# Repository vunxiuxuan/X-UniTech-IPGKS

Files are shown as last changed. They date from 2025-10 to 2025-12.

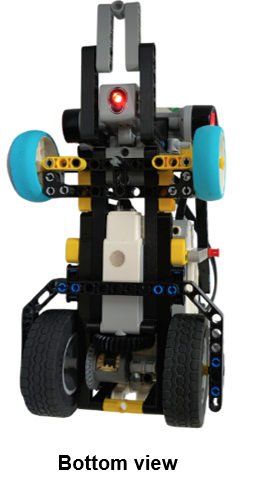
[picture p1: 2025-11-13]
v-photos/Bottom.png

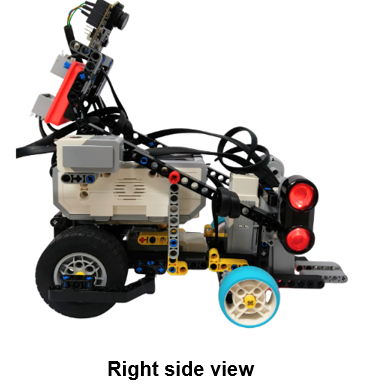
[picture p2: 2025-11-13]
v-photos/Right.png

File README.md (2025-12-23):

# Content (GitHub)
**schemes** This folder contains one or several schematic diagrams in the form of JPEG, PNG, or PDF of the electromechanical components illustrating all the elements (electronic components and motors) used in the vehicle and how they connect. This folder also included the schematic diagram of the robot for both open and obstacle challenge.

**src** This folder contains all the programming flowcharts and all programming used to participate in the WRO 2025 Future Engineers Category.

**t-photos** This folder contains photos of the team participating in the WRO 2025 Future Engineers Category.

**v-photos** This folder contains photos of the vehicle from all sides (top view, bottom view, front view, back view and side views)

**video** This folder contains video.md file that demonstrates how the robot functions to solve both challenges.

**models** This folder contains the robot building insturction and the 3D printed part building instruction that installed on the vehicle. The file is presented in .lxf, .ldr and .ldr format.

**other** This folder contains other files which can be used to understand how to prepare the vehicle for the competition.

Here attached with the link for our **COMPLETE DOCUMENTATION MODULE** (https://drive.google.com/file/d/107QRZqFFLUvLz7qMj4gl7RzuqnLO4l_k/view?usp=sharing)

# Table of Contents (Essay)
- [Introduction](#introduction)
- [X-UniTech Team, Malaysia](#x-unitech-team-malaysia)

- [1.0 Mobility Management](#10-mobility-management)
  - [1.1 Design of the self-driving car](#11-design-of-the-self-driving-car)
  - [1.2 Chassis of the self-driving car](#12-chassis-of-the-self-driving-car)

- [2.0 Power and Sense Management](#20-power-and-sense-management)
  - [2.1 Power source](#21-power-source)
  - [2.2 Sensor](#22-sensor)
  - [2.3 Build Of Materials (BOM)](#23-build-of-materials-bom)
  - [2.4 Wiring diagram](#24-wiring-diagram)

- [3.0 Obstacles Management](#30-obstacles-management)
  - [3.1 Open Challenge](#31-open-challenge)
  - [3.2 Obstacle Challenge](#32-obstacle-challenge)

- [4.0 Engineering Factors](#40-engineering-factors)
  
- [5.0 Improvements and Enhancements](#50-improvements-and-enhancements)
  - [5.1 Robot Construction](#51-robot-construction)
  - [5.2 Robot Programming](#52-robot-programming)

- [Credits](#credits)

# Introduction
This engineering documentation details comprehensive aspects of the car’s mobility management, power and sensor systems, obstacle detection and avoidance, construction design, integration of third-party sensors, and the improvements that were made throughout our preparation for the **World Robot Olympiad (WRO) International Final in Singapore 2025** under the Future Engineers Category.

# X-UniTech Team, Malaysia
X-UniTech is a team from Malaysia consisting of three-member engineering team specializing in the development of autonomous vehicles. Our team is responsible for the end-to-end design, construction, and integration of the vehicle's mechanical and electronic systems to ensure optimal performance. Let’s meet our members:

**Vun Xiu Xuan, Alvin Kong Wei Ee, and Grace Tan Hong Hui.**

Team Photo

# 1.0 Mobility Management
This section details the **mechanical design and propulsion system of our autonomous vehicle.** It covers the **chassis construction, component layout, and the integration of the motors.** Additionally, it introduces the fundamental engineering principles of speed, torque, and power that govern the vehicle's performance.

## 1.1 Design of the self-driving car
The autonomous self-driving car chassis and mechanical structure are built using the **Lego 45544 Mindstorms EV3 Education Set and various third-party sensors** such as **Pixy2 Camera** and **EV3 Multiplexer.**

Lego 45544 Mindstorms EV3 Education Set

The figures below show the autonomous vehicle we designed and constructed.  

**Top view**	

Robot (Top View)

**Bottom view** 

Robot (Bottom View)

**Front view**	

Robot (Front View)

**Back view** 

Robot (Back View)

**Left side view**	

Robot (Left Side View)

**Right side view** 

Robot (Right Side View)

## 1.2 Chassis of the self-driving car
The self-driving car chassis is designed to provide **structural support** and maintain **stability**, especially during high-speed maneuvers like sharp turns and rapid acceleration.

**(i) Selection of tyre**

For the front steering axle, we selected the **Medium Azure Hard Tyre** from the **Spike Essential** set because of its **hard rubber compound** that minimizes bouncing, allowing the vehicle **to track in a straight line** more reliably compared to softer tyres. The tyre's smaller diameter enables smoother and more precise steering corrections.

Medium Azure Hard Tyres

The rear axle is fitted with **LEGO MINDSTORMS EV3 tyres** (62.4 x 20 mm) on 43.2 mm rims. These tyres were selected for the excellent traction their tread pattern provides on typical competition surfaces, such as floors and mats. This high-grip design prevents wheel slippage during rapid acceleration and high-speed cornering. 

Lego Mindstorms EV3 Tyres

**(ii) Implementation of motor and its engineering principle**

Our self-driving car propulsion system consists of two EV3 Medium Motors mounted in a compact, orthogonal arrangement (one horizontal, one vertical). This design offers several key advantages: it optimizes internal space, simplifies the gear train assembly, and contributes to a low center of gravity. A low center of gravity is crucial for maintaining stability during the high-speed maneuvers required in the Open Challenge. 

EV3 Medium Motors

The diagram below illustrates the specifications and features of the EV3 Medium Motor.

Specifications of EV3 Medium Motor

The vehicle's steering mechanism is controlled by an **EV3 Medium Motor**, selected for its high responsiveness and precision. With a running torque of **8 Ncm** and a stall torque of **15 Ncm**, the motor provides ample force for steering control. Furthermore, its rotational speed of **260 rpm** allows quick rotations, making it well-suited for fine adjustments when avoiding traffic signs. 

 **(iii) Implementation of differential gear**
 
A differential gear is integrated into the drive axle, allowing the left and right wheels to **rotate at different speeds.** This mechanism is essential for executing smooth, controlled turns, as it prevents wheel binding and improves stability. This is particularly critical when navigating the tight corners found in the Open Challenge. Not only that, our robot also incorporates **a step-up gear ratio.** This setup makes the wheels spin **1.29 times faster** than the motor, increasing the speed from **260 RPM** at the motor to about **335 RPM** at the wheels. This helps the robot to move faster while at the same time maintaining stability during tight turns.

Differential Gear

**(iv) Engineering principle of steering**

The steering system is designed using **Ackermann steering geometry.** 

Ackermann Steering Geometry

This principle **turns the inner front wheel at a sharper angle** than the outer wheel, allowing both to follow ideal concentric turning circles. By minimizing lateral tire scrub, this geometry significantly reduces friction and wear. The primary benefits include enhanced cornering stability, improved traction, and the ability to execute sharp turns with greater precision.

**3D Printing Process Video**

3D Printing Process Video

https://youtu.be/b9eLe_nYFe0

# 2.0 Power and sense management
This section details the vehicle's **power source** and **sensor systems.** It covers the selection **rationale** and **implementation** of each sensor, along with an **analysis** of the **system's power consumption.** A **complete Build of Materials (BOM)** and **wiring diagram** are also provided for reference.

## 2.1 Power Source
The self-driving car is powered by a **Soshine 1.5V AA rechargeable lithium-ion (Li-ion) battery** with an energy capacity of 2600 mWh. This battery technology was selected for its stable voltage output, which ensures consistent and reliable performance for all electronic components.

Soshine Rechargeable AA Lithium-Ion Battery

## 2.2 Sensor
The self-driving car is designed to handle the diverse requirements of the Open and Obstacle Challenges. It includes **one color sensor, two ultrasonic sensors, one gyro sensor, and a Pixy2 camera.** The diagram below illustrates the placement and integration of these components.

Sensors

**(i) Pixy2 camera** 

The Pixy2 camera serves as the primary vision system for the vehicle during the Obstacle Challenge. Its main function is real-time object detection, allowing it to simultaneously **identify and track the red and green pillars** while the vehicle is in motion. It also helps to scan the magenta-colored parking zone to ensure the vehicle avoids this restricted area while navigating the course. The Pixy2 camera is mounted at a **65° angle** to provide optimal visibility when tracking traffic signs.

Pixy2 Camera

65° Pixy2 Camera

**(ii) Gyro sensor**

One gyro sensor is used to support our self-driving car. During both Open and Obstacle Challenge, it helps to **measure angles** and **maintain the correct heading** while driving. The gyro sensor also helps the robot to **turn at accurate angle** after passing the edge of the inner wall. While the gyro sensor can sometimes display errors at startup due to calibration issues, we resolved this by performing a hard reset before each run.

Gyro Sensor

**(iii) Ultrasonic sensor**

Our self-driving car is equipped with **two EV3 ultrasonic sensors.** These sensors measure the distance between the robot and wall **to avoid collision towards the walls.** The sensors operate by emitting sound waves and calculating the time it takes for them to bounce back after hitting a wall. This data enables the self-driving car to navigate efficiently, make accurate turns, and aim to complete the Open Challenge in the shortest time possible.

Ultrasonic Sensor

**(iv) Color sensor**

The colour sensor is only used in the Obstacle Challenge to **determine when the self-driving car should turn.** In a **clockwise** direction, the car **turns right** whenever it detects an orange line, while in a **counterclockwise** direction, it **turns left** upon detecting a blue line. The sensor functions by measuring the intensity of light entering it, allowing the car to identify colour lines and determine whether it is moving clockwise or counterclockwise. 

Color Sensor

## 2.3 Build of materials (BOM)

The table below shows the Build of Materials (BOM) used to build the self-driving car, making sure each part matches the car’s needs and functions.

Build of Materials (1)

Build of Materials (2)

Build of Materials (3)

Build of Materials (4)

Build of Materials (5)

Build of Materials (6)

## 2.4 Wiring diagram
The wiring diagram below illustrates the **sensors’ power consumption** and shows how the **motors and sensors are connected** within our self-driving car to support the setups for both the Open Challenge and the Obstacle Challenge. 

**(i) Open challenge wiring diagram**

Open Challenge Wiring Diagram

**(ii) Obstacle challenge wiring diagram**

Obstacle Challenge Wiring Diagram

# 3.0 Obstacles Management
In our project, we utilize the Clev3r-Python programming language to operate the robot. The programming structure is divided into two main sections which is the **Open Challenge** and the **Obstacle Challenge.** This section includes a flowchart and an overview of the code used for both challenges. 

## 3.1 Open Challenge
To complete the open challenge, our robot uses two main sensors which is an **EV3 Gyro Sensor** and **two EV3 Ultrasonic Sensors** on both the left and right sides. Since both **EV3 Ultrasonic Sensors** share the same port, we use a **multiplexer** to allow the robot to read data from each one separately. The left ultrasonic sensor is connected to Channel 2 of the multiplexer, while the right ultrasonic sensor is connected to Channel 3.

Gyro Sensor and Ultrasonic Sensor

The **EV3 Ultrasonic Sensors** helps the car to measure the distance between the robot and the walls. By comparing readings from the left and right sensors, the robot can determine whether it should move clockwise or counter clockwise. These readings also help the robot adjust its steering to avoid collisions and stay at a safe distance from inner and the outer walls. Additionally, the **EV3 Gyro Sensors** monitor the robot’s heading, ensuring it maintains a straight path and performs accurate turns at the correct angle when turning. 

Determine Direction (1)

In a quick overview, when the robot starts, it **first checks and sets up all its sensors.** Next, it **resets its steering** before moving. The robot then uses a **PID control system** to ensure smooth and stable turns. A drive function controls its speed and distance based on sensor data. Finally, the **main program** combines all these functions, enabling the robot to **follow walls, make precise turns,** and **complete all laps** efficiently and accurately. Further explanations of each function and programming part are provided in the **3.1.1 section below.**

Diagram below shows the flowchart for Open Challenge: 

Open Challenge Flow Chart

## 3.2 Obstacle Challenge
To complete the **Obstacle Challenge,** our robot utilizes four sensors which is **one Pixy2 Camera, one gyro sensor, two ultrasonic sensors** on both the left and right sides and **one colour sensor.** Since both ultrasonic sensors need to be connected to the same port, we use the **multiplexer** so that the robot can read data from both of the sensors.

Sensors

The **Pixy2 Camera** is connected to port 1 and it helps to detect the presence of pillars and magenta parking lot during the round. Next, the **EV3 Gyro Sensor** that connected to port 2 helps to ensures that the robot does the accurate turns and keep the robot’s heading straight during the round. In addition, both of the **EV3 Ultrasonic Sensor** is connected to EV3 Brick port 3 via the multiplexer. They help to detect the presence of the inner and outer wall and prevent the robot from hitting into the wall. Lastly, we utilize the **EV3 Colour Sensor** to identify the coloured line on the map which is the orange and blue line. The identified colour allows the robot to know the direction accurately. For instance, if orange line is scanned first, the direction will be in clockwise direction.

Here is the quick overview about the program. When the robot begins, it first **resets its steering mechanism** to ensure it starts from a centred and accurate position. As the robot drives, a **PID steering control system** is used to maintain stable movement and the correction such as gyro correction and keeping optimum distances from the outer wall. During the round, the **Drive function** continuously combines inputs from pillar detection, wall tracking, and PID correction. The sensors such as Pixy 2 Camera allows the robot **to identify traffic sign accurately** and choose the correct avoidance direction. After completing its last sections in the loop 12, the robot will **reverse to hit the wall** and aligns with the parking area and finally **performing a side parking neatly into the magenta parking zone.**

Diagram below shows the flowchart for **Obstacle Challenge:** 

Obstacle Challenge Flow Chart

# 4.0 Engineering Factors
This section showcases our **custom-designed and third-party open-source parts** along with detailed explanations of all the components installed in the car. 

At first, our autonomous self-driving car is **primarily built using the LEGO Mindstorms Education EV3 Core Set 45544.** However, we encountered several limitations while preparing for both the Open and Obstacle Challenges. For example, our design required more sensor ports than the EV3 brick could support, the **Pixy2 Camera was unstable** due to weak mounting, and we **lacked a suitable camera system** to accurately detect the pillars and the magenta parking lot. To overcome these challenges and enhance our robot’s performance, we incorporated **third-party components** into the design. The diagram below illustrates the additional components we used and how they helped overcome these issues.

**(i)	EV3 Sensor Multiplexer**

We added an EV3 Sensor Multiplexer so our robot can use five sensors at once. There are two ultrasonic sensors connected to the multiplexer with different channel. With all five working together, the robot can move more accurately and handle Obstacles Challenge better.

EV3 Sensor Multiplexer

**(ii)	3D Printed Part**

We created a 3D-printed casing for the chassis, steering and camera bracket to improve the robot’s overall performance. 

3D Printed Part

**(iii)	Pixy2 Camera**

We use the Pixy2 Camera because it can quickly and accurately detect objects while the robot is moving. In our design, the Pixy2 Camera is mainly used to scan and track the magenta parking lot, green and red pillars, which helps the robot recognize them in time and make the right navigation decisions during the Open and Obstacle Challenges.	. 
 
Pixy2 Camera

# 5.0 Improvements and Enhancements
In this section, we explain the **problems** we faced while building our self-driving car and the different **methods** we used to solve them. By studying each problem carefully, we made changes that improved the car performances. The improvements towards the robot can be categorized into two main parts which is the **construction** and **programming parts.**

## 5.1 Robot construction

We improved the construction of robot from time to time whenever we encountered challenges. Below are some of the improvements we implemented.

**(i)	Replace the front steering wheel with a smaller size wheel**

Initially, we are using the **LEGO tyre 44771** for the front wheel but then we switched to the smaller tyre from Spike Essential Set which is known as the **Medium Azure Hard Rubber Tyre.** The reduced size improved the car’s maneuverability, making it easier to turn and park in tight spaces. Moreover, the steering’s sensitivity is better when avoiding pillars.

Steering Wheel

## 5.2 Robot Programming

We refined the programming of our robot from time to time whenever we faced issues, making adjustments to improve its performance.

**(i)	Adding signal light to EV3 Brick**

At first, we did not connect the Pixy camera with the EV3 brick’s LED light. This made it **harder** to know when the robot had spotted a pillar. During testing, we had to **guess** whether the robot was reacting at the right time.

To make this easier for competition, we set the **LED to change colour when the robot sees a pillar.** By looking at the LED and the robot’s position on the map, we can **quickly** confirm if it is reacting **too early or too late.** We also thought about adding sound alerts, but in a crowded and noisy place, it would be **difficult to hear** them. That’s why using lights is a better choice to overcome the problems.

Signal Light

# Credits

We extend our sincere appreciation to our key supporters. Special thanks to LEGO Education for their generous provision of high-quality EV3 and SPIKE Essential sets. We are also grateful to Bambu Lab, whose advanced 3D printing technology was instrumental in the development of our custom components.

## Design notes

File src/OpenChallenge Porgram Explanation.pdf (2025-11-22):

### 3.1 Open Challenge

To complete the open challenge, our robot uses two main sensors which is an EV3 Gyro

Sensor and two EV3 Ultrasonic Sensors on both the left and right sides. Since both EV3

Ultrasonic Sensors share the same port, we use a multiplexer to allow the robot to read

data from each one separately. The left ultrasonic sensor is connected to Channel 2 of the

multiplexer, while the right ultrasonic sensor is connected to Channel 3.

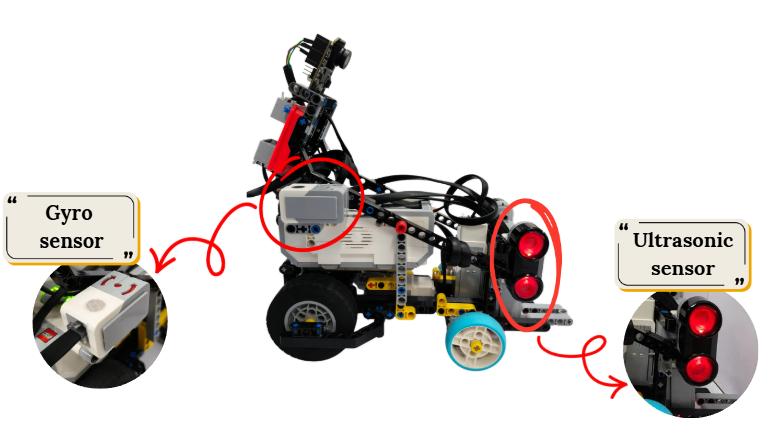
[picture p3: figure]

The EV3 Ultrasonic Sensors helps the car to measure the distance between the robot

and the walls. By comparing readings from the left and right sensors, the robot can determine

whether it should move clockwise or counter clockwise. These readings also help the robot

adjust its steering to avoid collisions and stay at a safe distance from inner and the outer walls.

Additionally, the EV3 Gyro Sensors monitor the robot’s heading, ensuring it maintains a

straight path and performs accurate turns at the correct angle when turning.

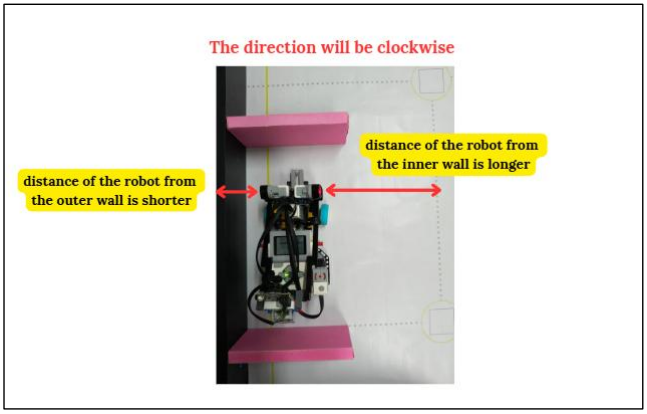
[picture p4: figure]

In a quick overview, when the robot starts, it first checks and sets up all its sensors.

Next, it resets its steering before moving. The robot then uses a PID control system to

ensure smooth and stable turns. A drive function controls its speed and distance based on

sensor data. Finally, the main program combines all these functions, enabling the robot to

follow walls, make precise turns, and complete all laps efficiently and accurately. Further

explanations of each function and programming part are provided in the 3.1.1 section below.

Diagram below shows the flowchart for Open Challenge:

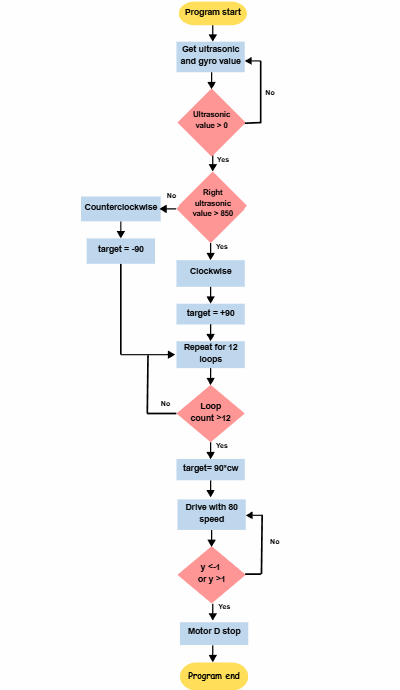
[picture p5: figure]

Appendix 2 contains the complete programming code for the Open Challenge.

### 3.1.1 Coding explanation

Below is a brief explanation of the key parts of the code used to control the robot during the

challenge.

(a) Initialization and Setup

This part is aim to set up the sensors and multiplexer before running. The

setMultiplexerMode function allows the EV3 to connect with both ultrasonic sensors

in the same port while the getMultiplexerValues function allows the robot to read the

distance values from the left and right ultrasonic sensors. Additionally, the

ReadSensor continuously updates the robot’s heading and wall distances in real time.

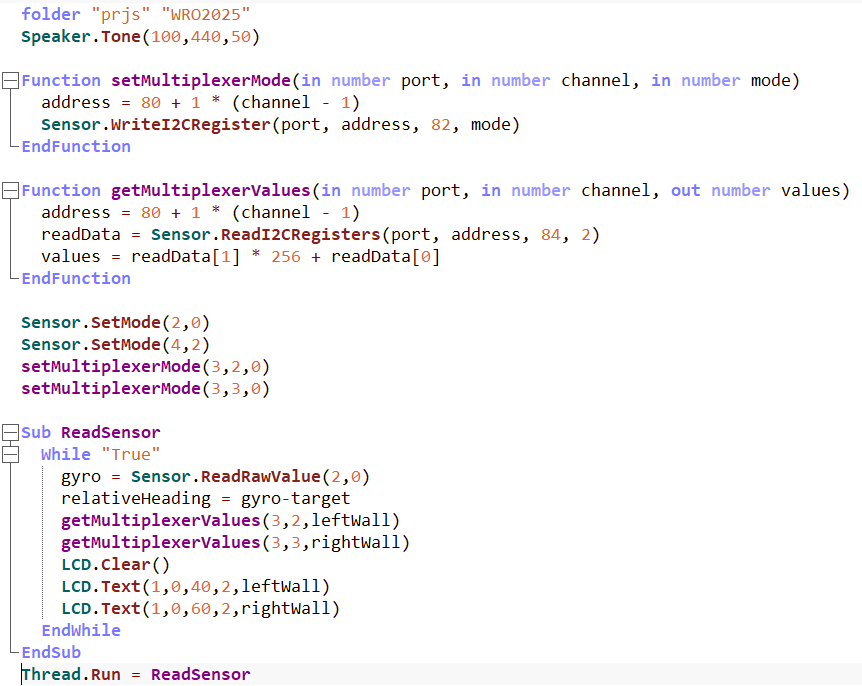
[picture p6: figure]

(b) Car Position Coordinate Tracking

This part of the program is about position tracking using a gyro sensor and motor

speed. It continuously calculates the robot’s position on the X and Y axis based on

how fast the motor is spinning and the angle detected by the gyro sensor. The

Math.Sin and Math.Cos functions are used to determine the direction of movement,

converting the robot’s rotation into horizontal (x) and vertical (y) changes. The program keeps updating these values in real time, showing them on the LCD screen.

To prevent errors, it also limits both the X and Y positions to a range between -20 and

### 20. In simple terms, this part allows the robot to “know” where it is moving by combining

speed and direction data, then displays its current position on the screen.

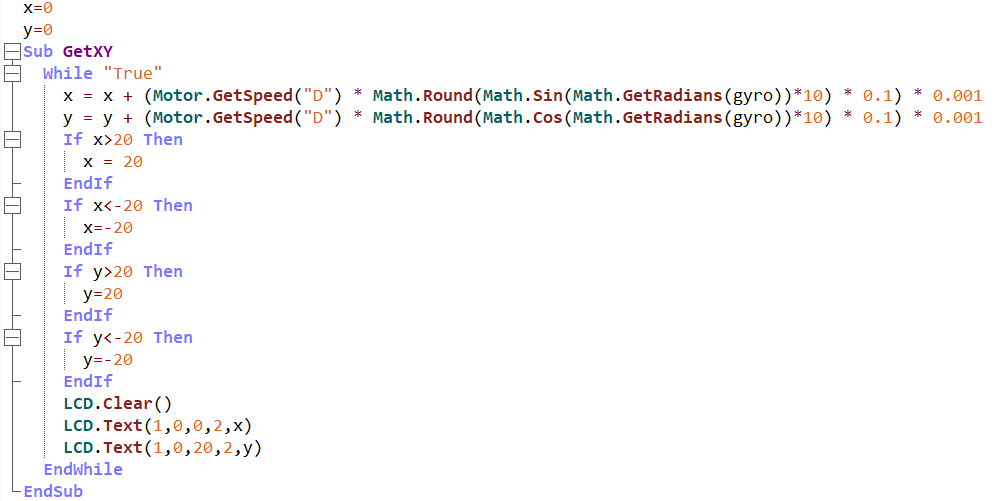
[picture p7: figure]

(c) Reset Steering

Reset Steering make sure the steering motor starts at a fixed desired position before

driving. The robot turns the steering motor all the way to the left for 300 milliseconds

by using the medium motor in the port A. Hence, it waits until the motor completely

stops moving, which means it has hit the limit. After that, the motor’s rotation is reset

to zero. This step is important because it gives the information to the robot exactly

where the “straight ahead” position is.

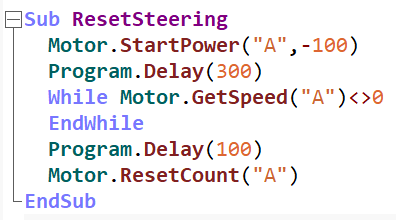
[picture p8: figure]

(d) PID Steering Control

The PID Steering function helps the robot to adjust the steering motor whenever it

starts to drift off from the target. The P part fixes most of the error right away, the I

part makes small adjustments over time and the D part make sure that the correction

is done smoothly. These three adjustments are added together to get one correction

value, which is sent to motor A to turn the steering. This keeps the robot moving

smoothly, avoiding zig-zagging, and makes its turns more accurate.

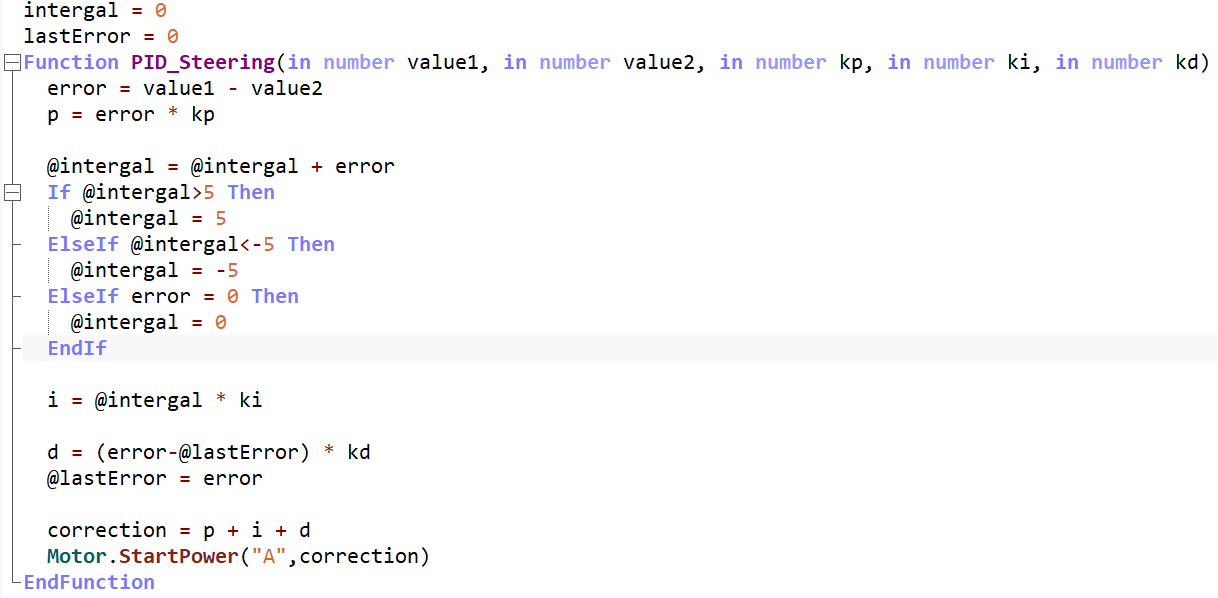
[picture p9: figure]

(e) Drive

Function Drive controls how the robot drives and follows a wall. First, it checks

whether the ultrasonic sensors on both sides are working. If either sensor is not

detecting a wall (value = 0), the robot stops moving. This acts as a safety feature,

ensuring the robot doesn’t move blindly when there is no sensor data. If both sensors

are working, the robot moves forward at the given speed.

Next, when wall tracking (trackWall) is turned on, the robot adjusts its direction to

stay at the correct distance from the wall. If the robot is moving clockwise, it uses the

right sensor; if moving counterclockwise, it uses the left sensor. It calculates how

much the robot needs to turn to maintain the proper distance and making sure it’s not

too close or too far. If the error is more than or less than 40 based on the robot’s

distance and the inner wall, it will perform a correction to the steering. Finally, a PID

steering control ensures smooth and precise turns based on this calculation, keeping

the robot aligned while following the wall safely.

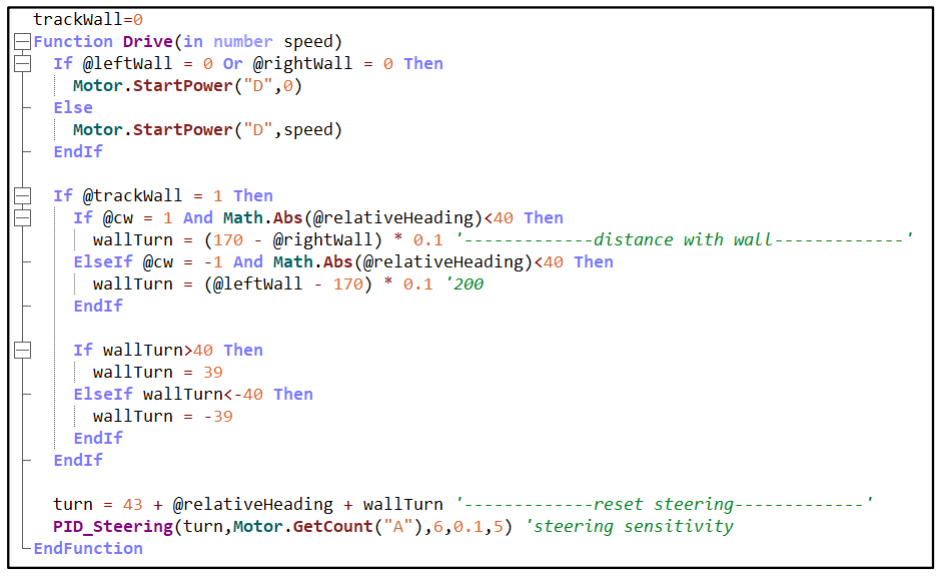
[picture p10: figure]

Moreover, the DriveDegrees function moves the robot forward in rotation

degrees. He robot will keep driving at the given speed until the target degrees are

reached, and stops the motor if stop is set to 1.

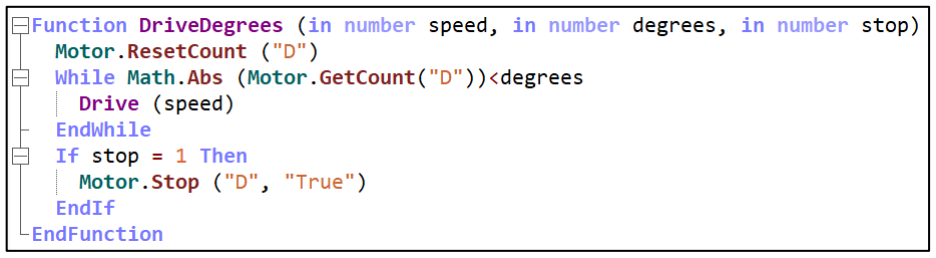
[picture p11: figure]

(f) Main program

This program resets timers and steering, then drives forward until it detects a wall on

either side. It determines whether to follow the right or left wall based on sensor

readings.

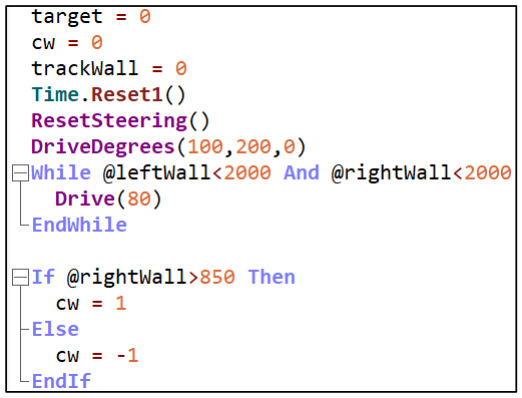
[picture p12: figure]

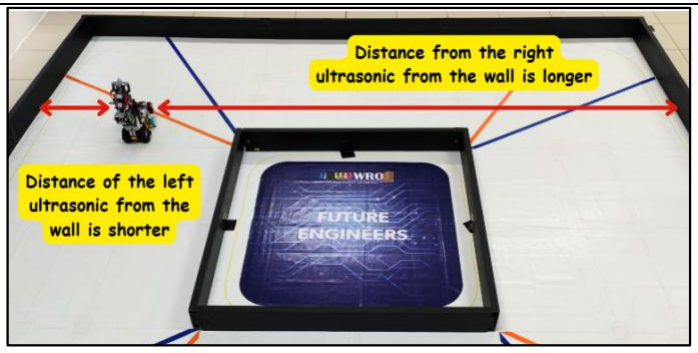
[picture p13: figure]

The robot will move in

clockwise direction.

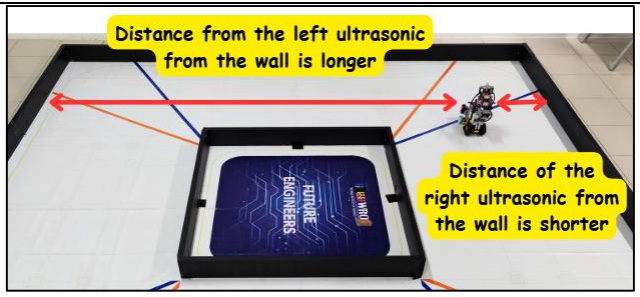
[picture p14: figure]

The robot will move in

counter clockwise direction.

When the robot enters the second section, it does not immediately start wall

tracking. Instead, it first drives a certain distance in degrees before activating wall

tracking. This is done to prevent sudden corrections. If the robot starts tracking the

wall when the sensor values are far from the desired distance, it could make a sharp

turn and accidentally hit the wall. After driving the initial distance, wall tracking

(trackWall) is turned on, and the robot begins adjusting its direction to follow the wall

smoothly. While tracking, the robot moves at a controlled speed of 80, which ensures

stable motion and reduces the risk of collisions as it approaches the wall.

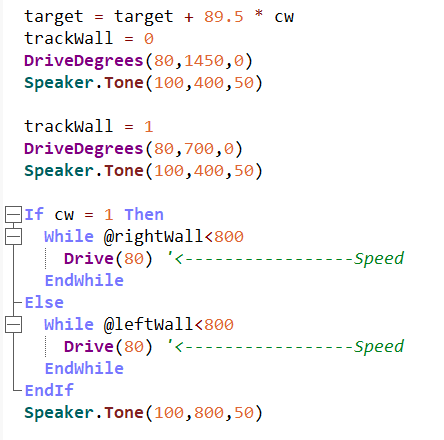
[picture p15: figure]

Then, it loops the same program for 10 times, turning 90° in the chosen

direction in every loops. After completing the 10 loops, the robot enters the last

section. It updates the target from time to time and drives forward while checking the

Y-coordinate until it is roughly within the range -1 to 1, which represent that the robot will stop at the (0,0) position. Once there, the robot stops all motors and pauses for

2.5 seconds to complete the task.

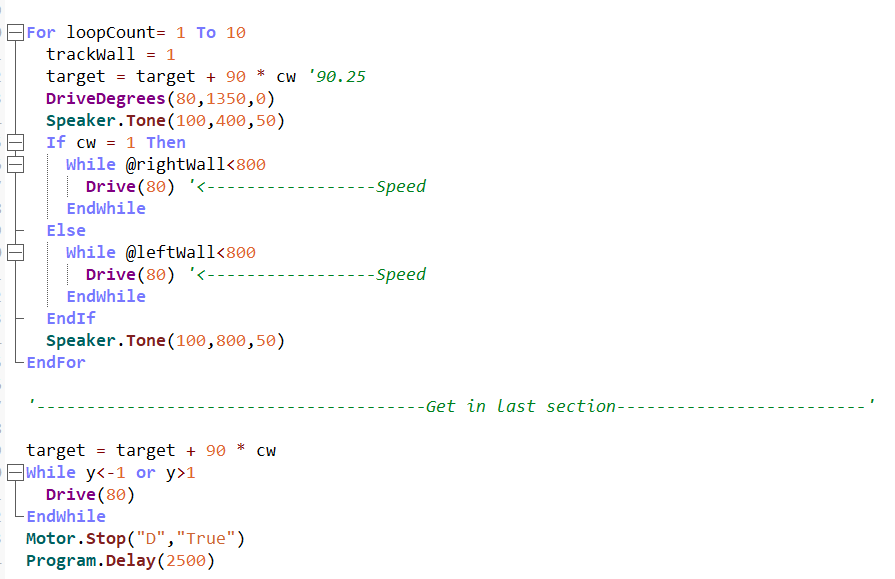
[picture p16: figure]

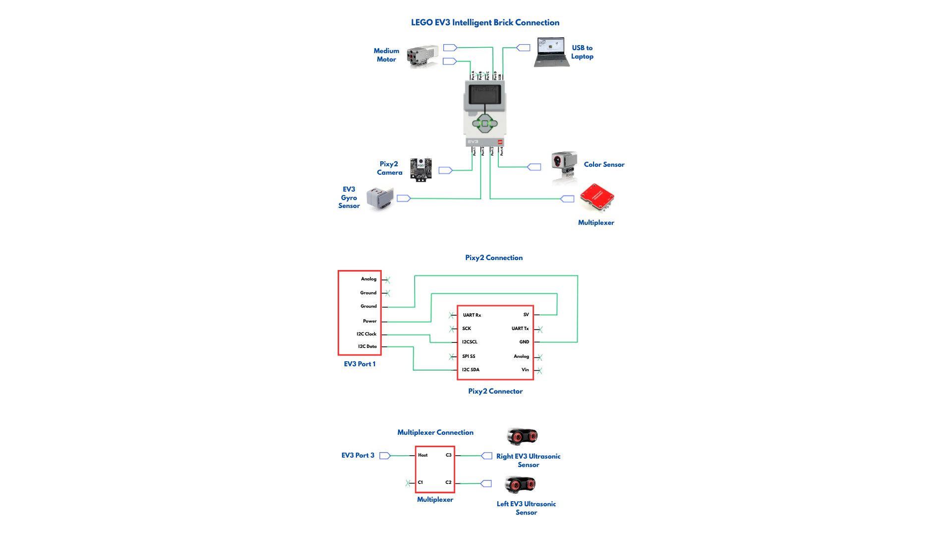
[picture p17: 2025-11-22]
schemes/ObstacleChallenge_SchematicDiagram.png

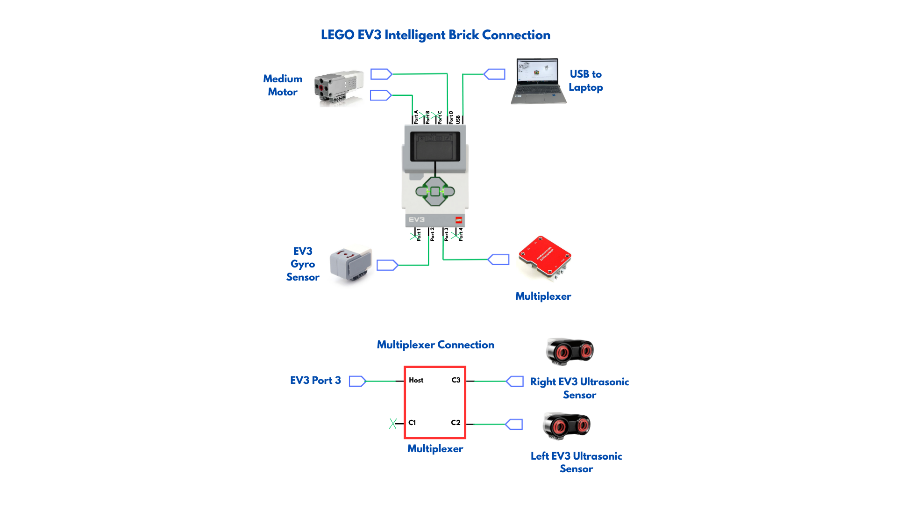
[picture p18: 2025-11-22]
schemes/OpenChallenge_SchematicDiagram.png

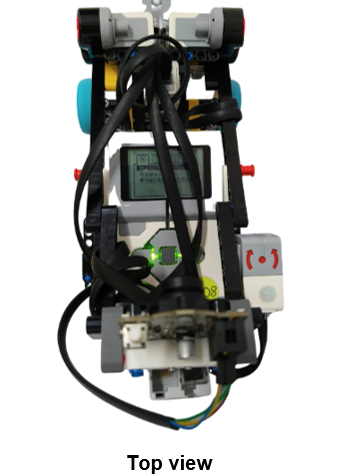
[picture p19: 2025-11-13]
v-photos/Top.png

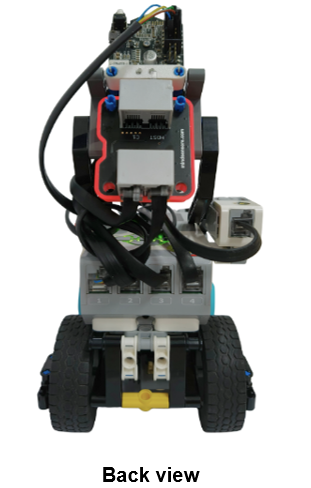
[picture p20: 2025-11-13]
v-photos/back.png

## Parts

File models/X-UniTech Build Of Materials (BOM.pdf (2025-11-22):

No. | Brick | Name | Picture | Part | Color Code | Quantity
1 | - | LEGO WHEEL Ø43 WITH MEDIUM AZURE TIRE | | 65834 | 6285433 | 2
2 | 4551421 | RIM Ø 43,2 X 18 | | 86652 | 194 - Medium Stone Grey | 2
3 | 4107806 | TYRE Ø 62,4X20 | | 32019 | 26 - Black | 2
4 | 6008919 | MS, EV3, SENSOR, COLOUR | | 95650 | 194 - Medium Stone Grey, 1 - White, 26 -Black, 102 - Medium Blue, 21 - Bright Red | 1
5 | 6008916 | MS, EV3, GYRO SENSOR | | 99380 | 194 - Medium Stone Grey, 1 - White, 315 - Silver Metallic, 21 -Bright Red | 1
6 | 6008577 | SMALL MOTOR | | 99455 | 21 - Bright Red, 194 - Medium Stone Grey, 1 - White, 315 - Silver Metallic | 2
7 | 6063629 | MS-EV3, ULTRASONIC SENSOR | | 95652 | 194 - Medium Stone Grey, 1 - White, 26 -Black, 41 - Tr. Red, 315 - Silver Metallic | 2
8 | 6009996 | MS-EV3, P-BRICK | | 95646 | 1 - White, 194 -Medium Stone Grey, 40 - Transparent, 199 - Dark Stone Grey, 315 - Silver Metallic | 1
9 | 4142822 | TECHNIC 3M BEAM | | 32523 | 26 - Black | 2

10 | 4211655 | TECHNIC 3M BEAM | 32523 | 194 - Medium Stone Grey | 1
11 | 4153718 | TECHNIC 3M BEAM | 32523 | 21 - Bright Red | 2
12 | 4140429 | TECHNIC 5M BEAM | 32316 | 26 - Black | 2
13 | 4211651 | TECHNIC 5M BEAM | 32316 | 194 - Medium Stone Grey | 2
14 | - | TECHNIC 7M BEAM | 32524 | 322 - Medium Azur | 2
15 | 3252426 | TECHNIC 7M BEAM | 32524 | 26 - Black | 1
16 | 4495930 | TECHNIC 7M BEAM | 32524 | 194 - Medium Stone Grey | 2
17 | 4141628 | TECHNIC ANG. BEAM 4X2 90 DEG | 32140 | 24 - Bright Yellow | 8
18 | - | TECHNIC 9M BEAM | 40490 | 26 - Black | 5
19 | - | T-BEAM 3X3 W/HOLE Ø4.8 | 60484 | 24 - Bright Yellow | 2

20 | 4535771 | T-BEAM 3X3 W/HOLE Ø4.8 | 60484 | 26 - Black | 2
21 | 4542573 | TECHNIC 15M BEAM | 32278 | 26 - Black | 4
22 | 4210753 | TECHNIC ANG. BEAM 3X5 90 DEG. | 32526 | 199 - Dark Stone Grey | 4
23 | 4107578 | DOUBLE ANGULAR BEAM 3X7 45° | 32009 | 26 - Black | 4
25 | 4239601 | 1/2 BUSH | 32123 | 24 - Bright Yellow | 6
26 | 4142865 | 2M CROSS AXLE W. GROOVE | 32062 | 21 - Bright Red | 3
27 | 278026 | CONNECTOR PEG W. FRICTION | 2780 | 26 - Black | 56
28 | 4211807 | CONNECTOR PEG | 3673 | 194 - Medium Stone Grey | 4
29 | 4211815 | CROSS AXLE 3M | 4519 | 194 - Medium Stone Grey | 3
30 | 4225927 | CONNECTOR PEG/CROSS AXLE | 6562 | 23 - Bright Blue | 22

31 | 4211622 | CROSS AXLE BUSH FOR | 6590 | 194 - Medium Stone Grey | 4
32 | 4514553 | CONNECTOR PEG W. FRICTION 3M | 6558 | 23 - Bright Blue | 11
33 | - | CROSS AXLE 2M W. SNAP W. FRIC. | 18651 | 26 - Black | 2
34 | 4566927 | CROSSAXLE 3M WITH KNOB | 6587 | 138 - Sand Yellow | 2
35 | 653626 | CROSS BLOCK 90° | 6536 | 26 - Black | 2
36 | 4107085 | ANGLE ELEMENT, 0 DEGREES [1] | 32013 | 26 - Black | 2
37 | 370626 | CROSS AXLE 6M | 3706 | 26 - Black | 2
38 | 4125198 | 2M FRIC. SNAP W/CROSS HOLE | 32054 | 21 - Bright Red | 2
39 | 4185111 | CROSS AXLE 7M | 44294 | 26 - Black | 2
40 | 4121667 | DOUBLE CROSS BLOCK | 32184 | 26 - Black | 4

41 | 3218401 | DOUBLE CROSS BLOCK | 32184 | 1 - White | 2
42 | 370726 | CROSS AXLE 8M | 3707 | 26 - Black | 1
43 | 3203424 | ANGLE ELEMENT, 180 DEGREES [2] | 32034 | 24 - Bright Yellow | 1
44 | 4560175 | DOUBLE BUSH 3M Ø4.9 | 87082 | 194 - Medium Stone Grey | 1
45 | 4156980 | 2X1X3 STEERING KNUCKLE ARM | 33299 | 26 - Black | 1
46 | 4119589 | MODULE BUSH | 32138 | 26 - Black | 2
47 | 4538007 | CROSS BLOCK 3X2 | 63869 | 194 - Medium Stone Grey | 1
48 | 4225033 | BEAM 3 M. W/4 SNAPS | 48989 | 194 - Medium Stone Grey | 2
49 | 4296059 | ANGULAR BEAM 90DEGR. W.4 SNAPS | 55615 | 194 - Medium Stone Grey | 2
50 | - | BEAM FRAME 5X7 Ø 4.85 | 64179 | 26 - Black | 1

51 | 4140445 | CONICAL WHEEL Z12 | 6589 | 5 - Brick Yellow | 3
52 | 4177434 | DOUBLE CONICAL WHEEL Z36 | 32498 | 26 - Black | 1
53 | 4525184 | DIFFERENTIALE 3M Z 28 | 62821 | 199 - Dark Stone Grey | 1
54 | - | PIXY 2 CAMERA (THIRD PARTY SENSOR | - | - | 1
55 | - | EV3 SENSOR MULTIPLEXER (THIRD PARTY SENSOR) | - | - | 1
Total: | | | | | 204

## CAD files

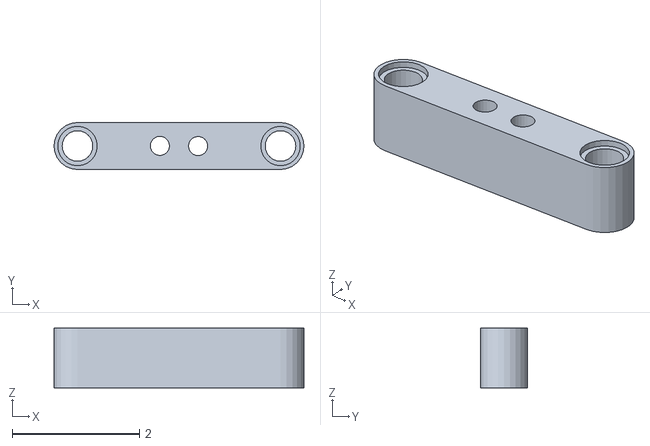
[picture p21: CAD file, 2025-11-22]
models/3DPritned_PixyHolder.obj
3.93 x 0.738 x 0.936

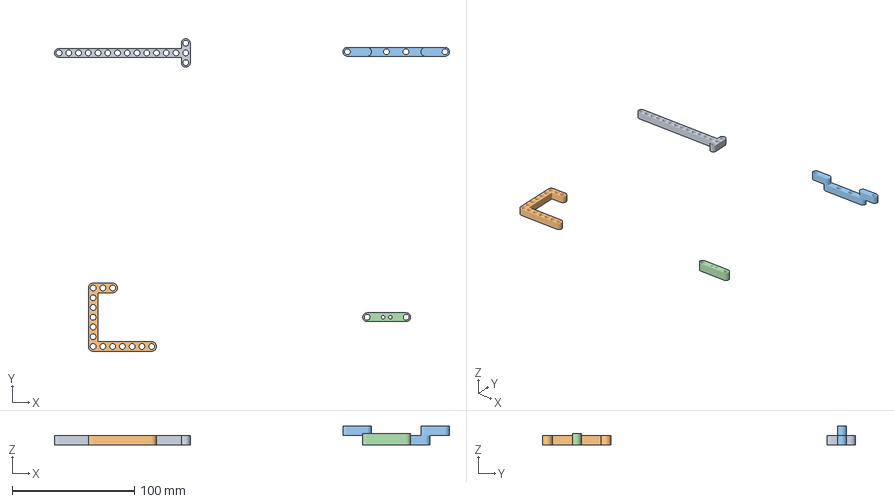
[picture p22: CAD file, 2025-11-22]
models/3DPrinted_PixyHolder.3mf
322.8 x 255.6 x 15.5 mm
Pixy Holder v2.obj

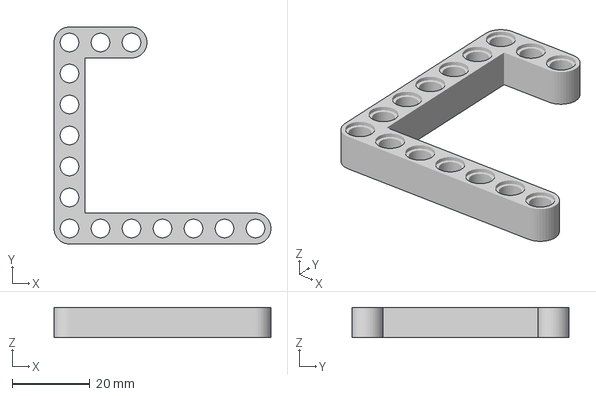
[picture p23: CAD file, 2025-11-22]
models/3DPrinted_Front.3mf
55.8 x 55.8 x 7.76 mm

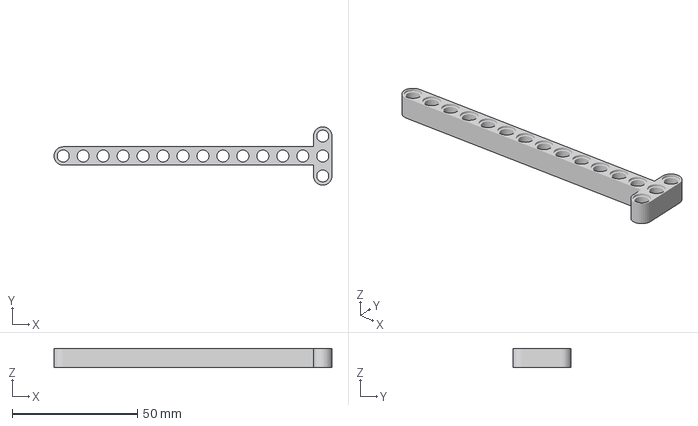
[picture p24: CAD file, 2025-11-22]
models/3DPrinted_Chassis.3mf
111.0 x 23.3 x 7.76 mm

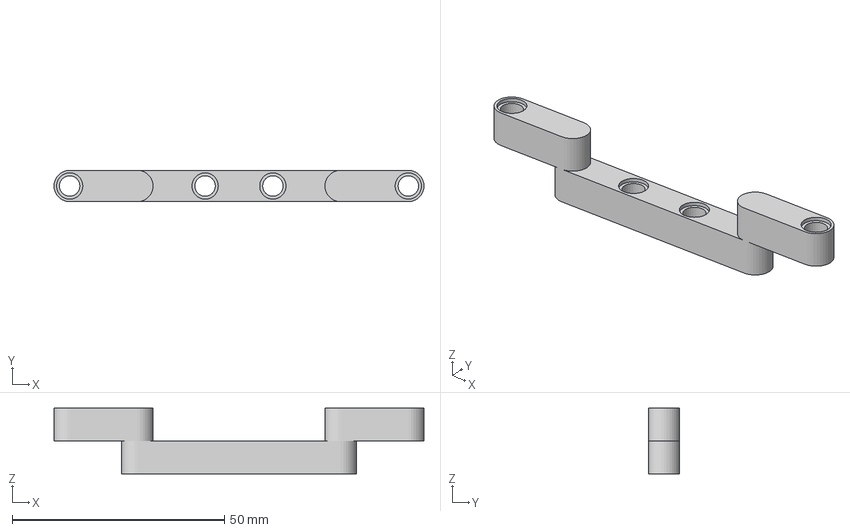
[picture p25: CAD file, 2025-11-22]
models/3DPrinted_Steering.3mf
87.1 x 7.38 x 15.5 mm

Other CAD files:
models/3DPrinted_Chassis.stl
models/3DPrinted_Front.stl
models/3DPrinted_Steering.stl

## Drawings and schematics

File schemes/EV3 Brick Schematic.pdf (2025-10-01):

# Ram Flash

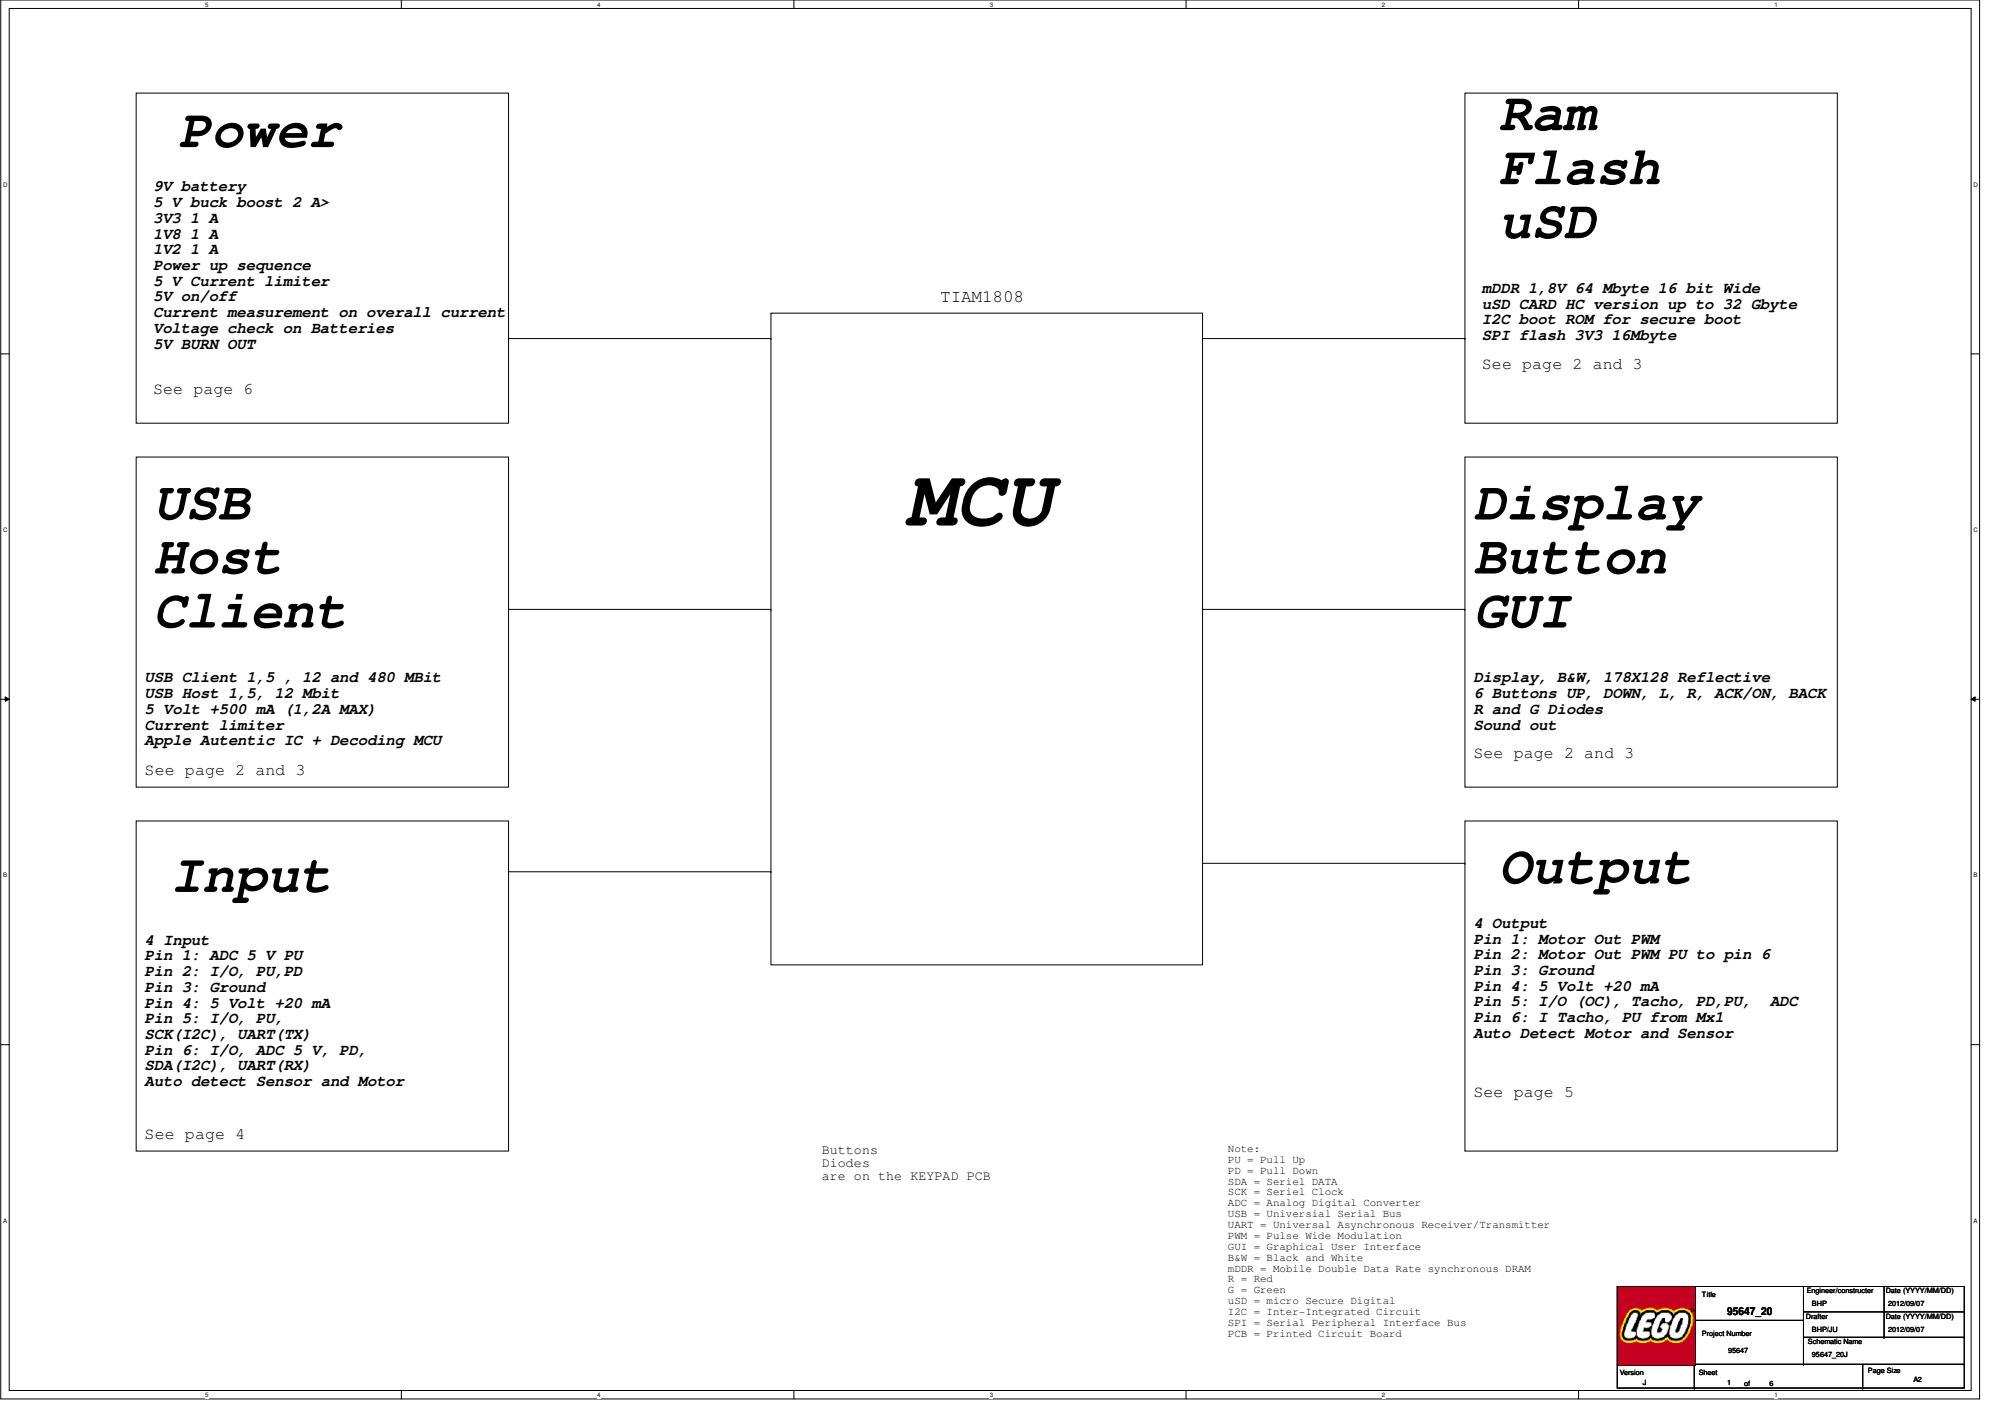
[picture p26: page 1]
MCU; uSD; Display Button GUI; Output; Power; USB Host Client; Pin 5: I/O (OC), Tacho, PD,PU,; ADC; TIAM1808; See page 6; See page 4; See page 5; Title; Project Number; Engineer/constructer; Schematic Name; Drafter; Date (YYYY/MM/DD); Version; Sheet; Page Size; BHP; BHP/JU

9V battery
5 V buck boost 2 A>
Power up sequence
5 V Current limiter
5V on/off
Current measurement on overall current
Voltage check on Batteries
5V BURN OUT

mDDR 1,8V 64 Mbyte 16 bit Wide
uSD CARD HC version up to 32 Gbyte
I2C boot ROM for secure boot
SPI flash 3V3 16Mbyte

See page 2 and 3

USB Client 1,5 , 12 and 480 MBit
USB Host 1,5, 12 Mbit
5 Volt +500 mA (1,2A MAX)
Current limiter
Apple Autentic IC + Decoding MCU

Display, B&W, 178X128 Reflective
6 Buttons UP, DOWN, L, R, ACK/ON, BACK
R and G Diodes
Sound out

Input

4 Output
Pin 1: Motor Out PWM
Pin 2: Motor Out PWM PU to pin 6
Pin 3: Ground
Pin 4: 5 Volt +20 mA
Pin 6: I Tacho, PU from Mx1
Auto Detect Motor and Sensor

4 Input
Pin 1: ADC 5 V PU
Pin 2: I/O, PU,PD
Pin 5: I/O, PU,
SCK(I2C), UART(TX)
Pin 6: I/O, ADC 5 V, PD,
SDA(I2C), UART(RX)
Auto detect Sensor and Motor

Buttons
Diodes
are on the KEYPAD PCB

Note:
PU = Pull Up
PD = Pull Down
SDA = Seriel DATA
SCK = Seriel Clock
ADC = Analog Digital Converter
USB = Universial Serial Bus
UART = Universal Asynchronous Receiver/Transmitter
PWM = Pulse Wide Modulation
GUI = Graphical User Interface
B&W = Black and White
mDDR = Mobile Double Data Rate synchronous DRAM
R = Red
G = Green
uSD = micro Secure Digital
I2C = Inter-Integrated Circuit
SPI = Serial Peripheral Interface Bus
PCB = Printed Circuit Board

Date (YYYY/MM/DD)

D

D

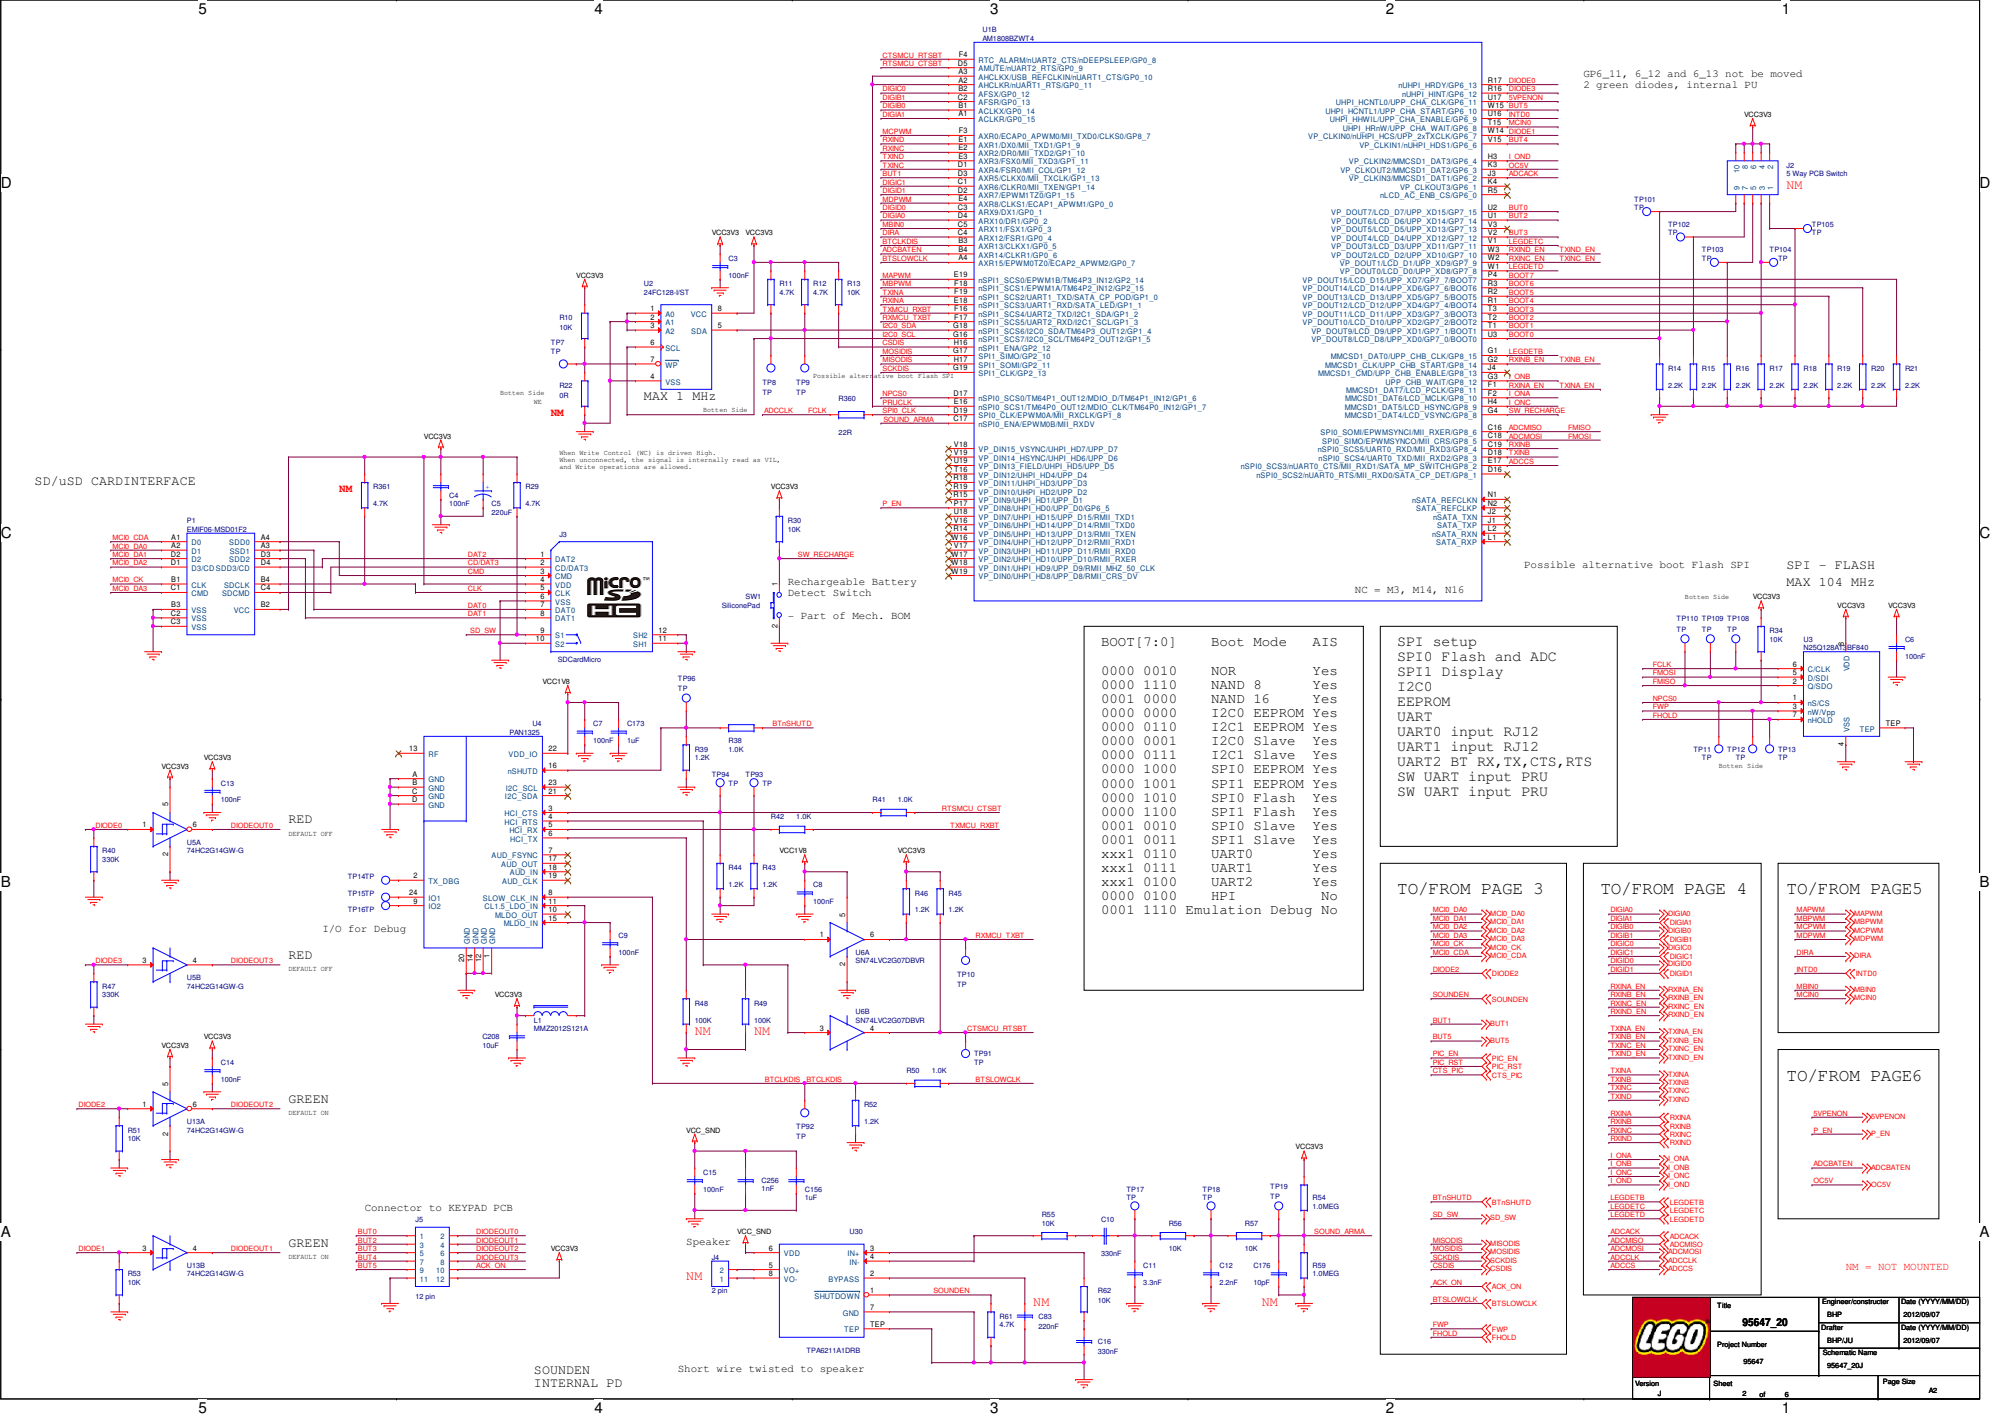
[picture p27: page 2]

GP6_11, 6_12 and 6_13 not be moved
2 green diodes, internal PU

Possible alternative boot Flash SPI

When Write Control (WC) is driven High.
When unconnected, the signal is internally read as VIL,
and Write operations are allowed.

CMD | 3

- Part of Mech. BOM

SW UART input PRU

Connector to KEYPAD PCB

Short wire twisted to speaker

D

D

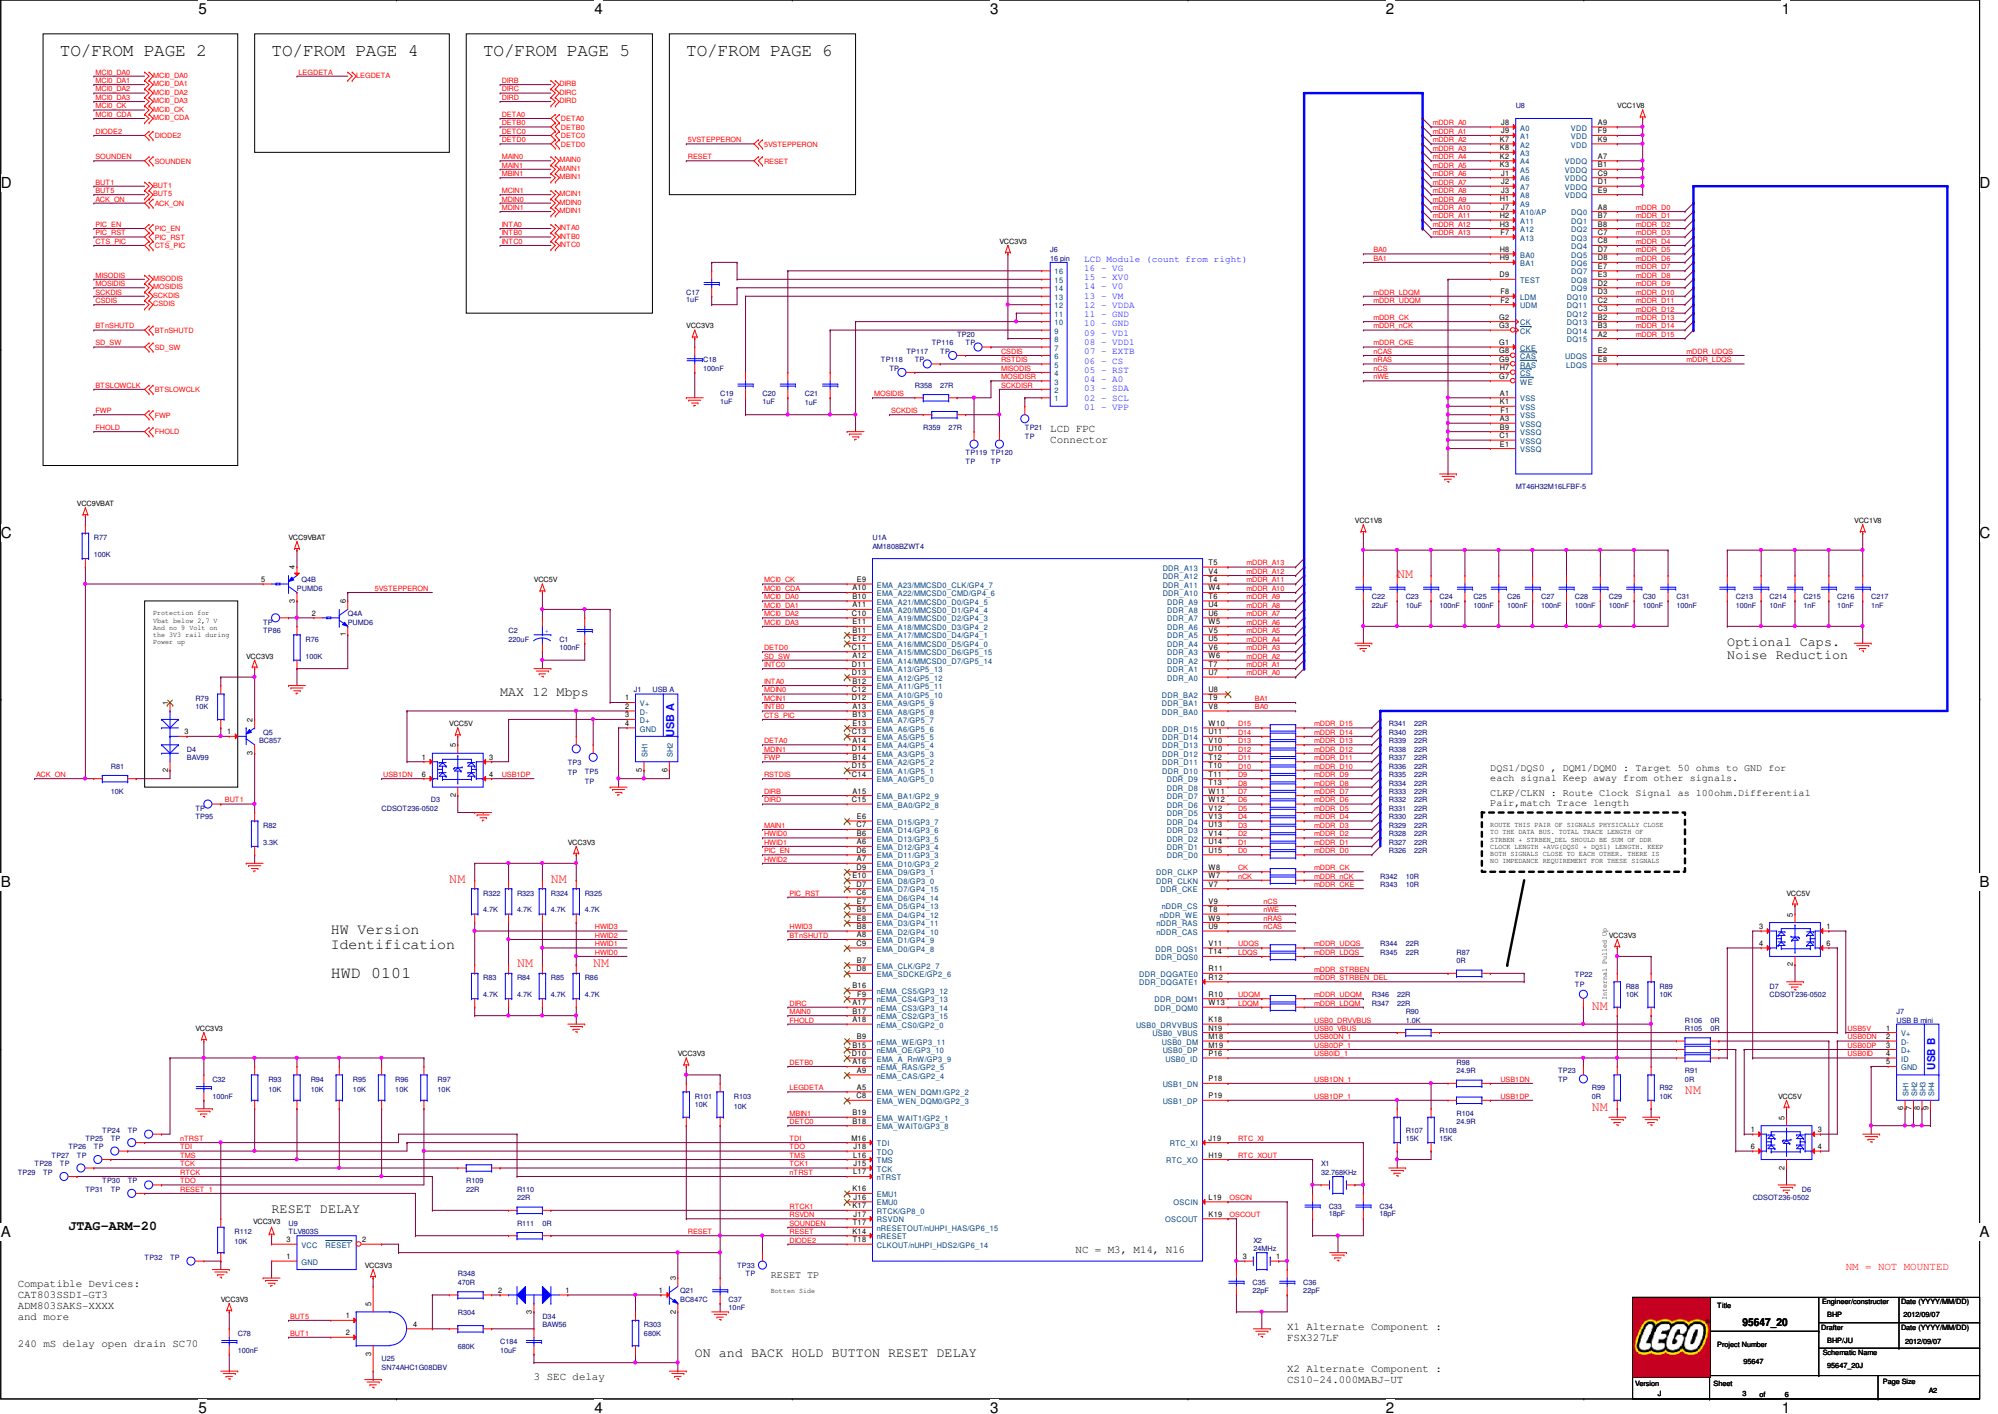
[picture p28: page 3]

Protection for
Vbat below 2,7 V
And no 9 Volt on
the 3V3 rail during
Power up

DQS1/DQS0 , DQM1/DQM0 : Target 50 ohms to GND for
each signal Keep away from other signals.
CLKP/CLKN : Route Clock Signal as 100ohm.Differential
Pair,match Trace length

ROUTE THIS PAIR OF SIGNALS PHYSICALLY CLOSE
TO THE DATA BUS. TOTAL TRACE LENGTH OF
STRBEN + STRBEN_DEL SHOULD BE SUM OF DDR
CLOCK LENGTH +AVG(DQS0 + DQS1) LENGTH. KEEP
BOTH SIGNALS CLOSE TO EACH OTHER. THERE IS
NO IMPEDANCE REQUIREMENT FOR THESE SIGNALS

240 mS delay open drain SC70

ON and BACK HOLD BUTTON RESET DELAY

D | D

# INPUT A

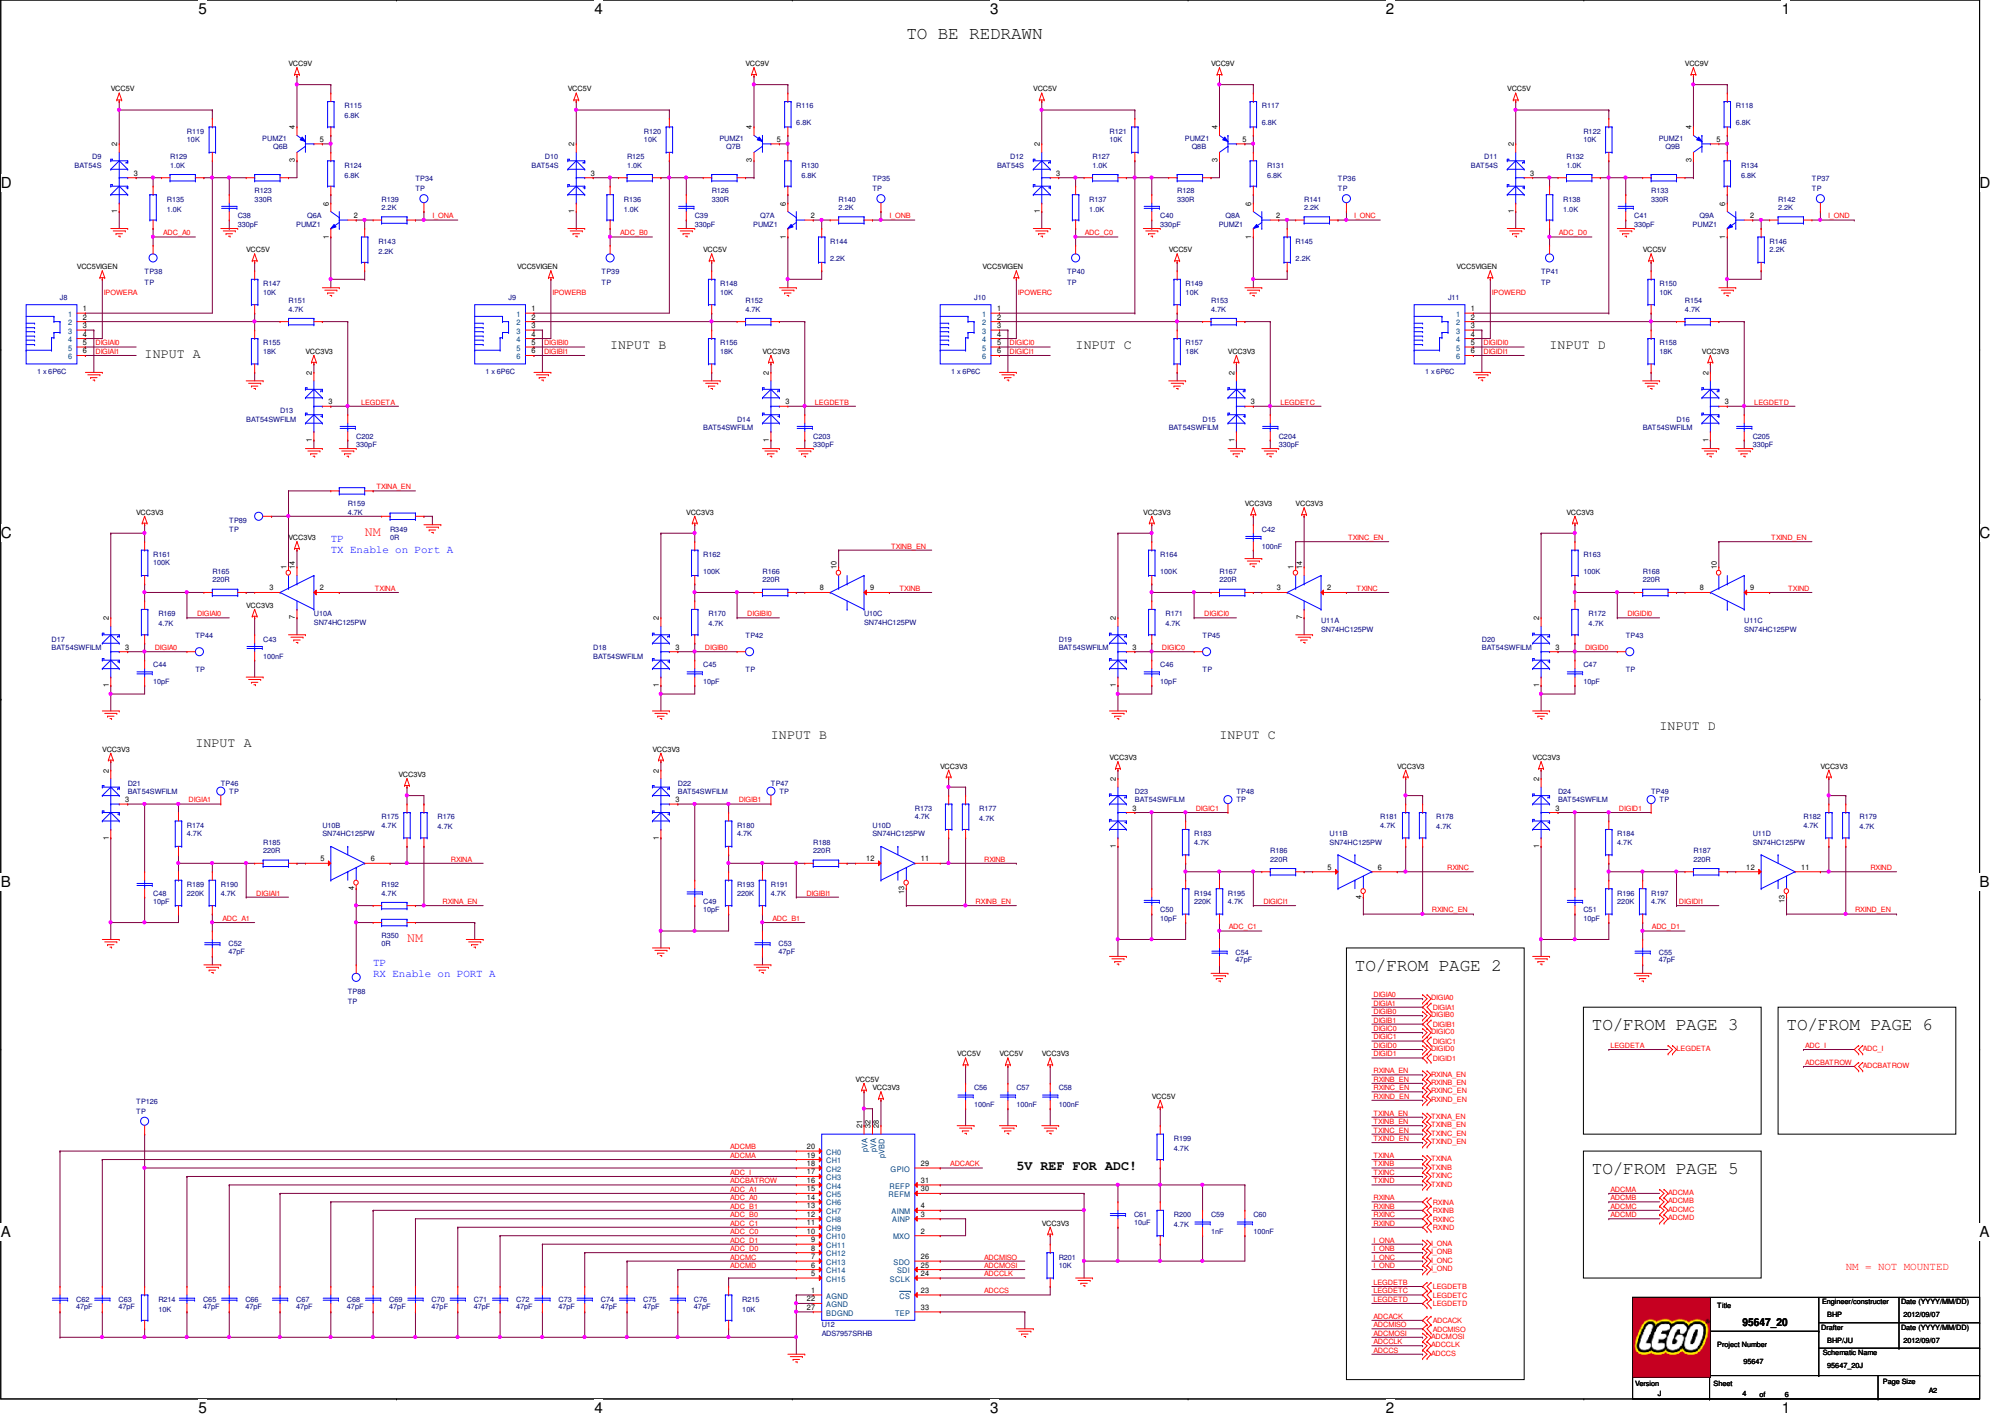
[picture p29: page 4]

TX Enable on Port A

## MotorA

## MotorB

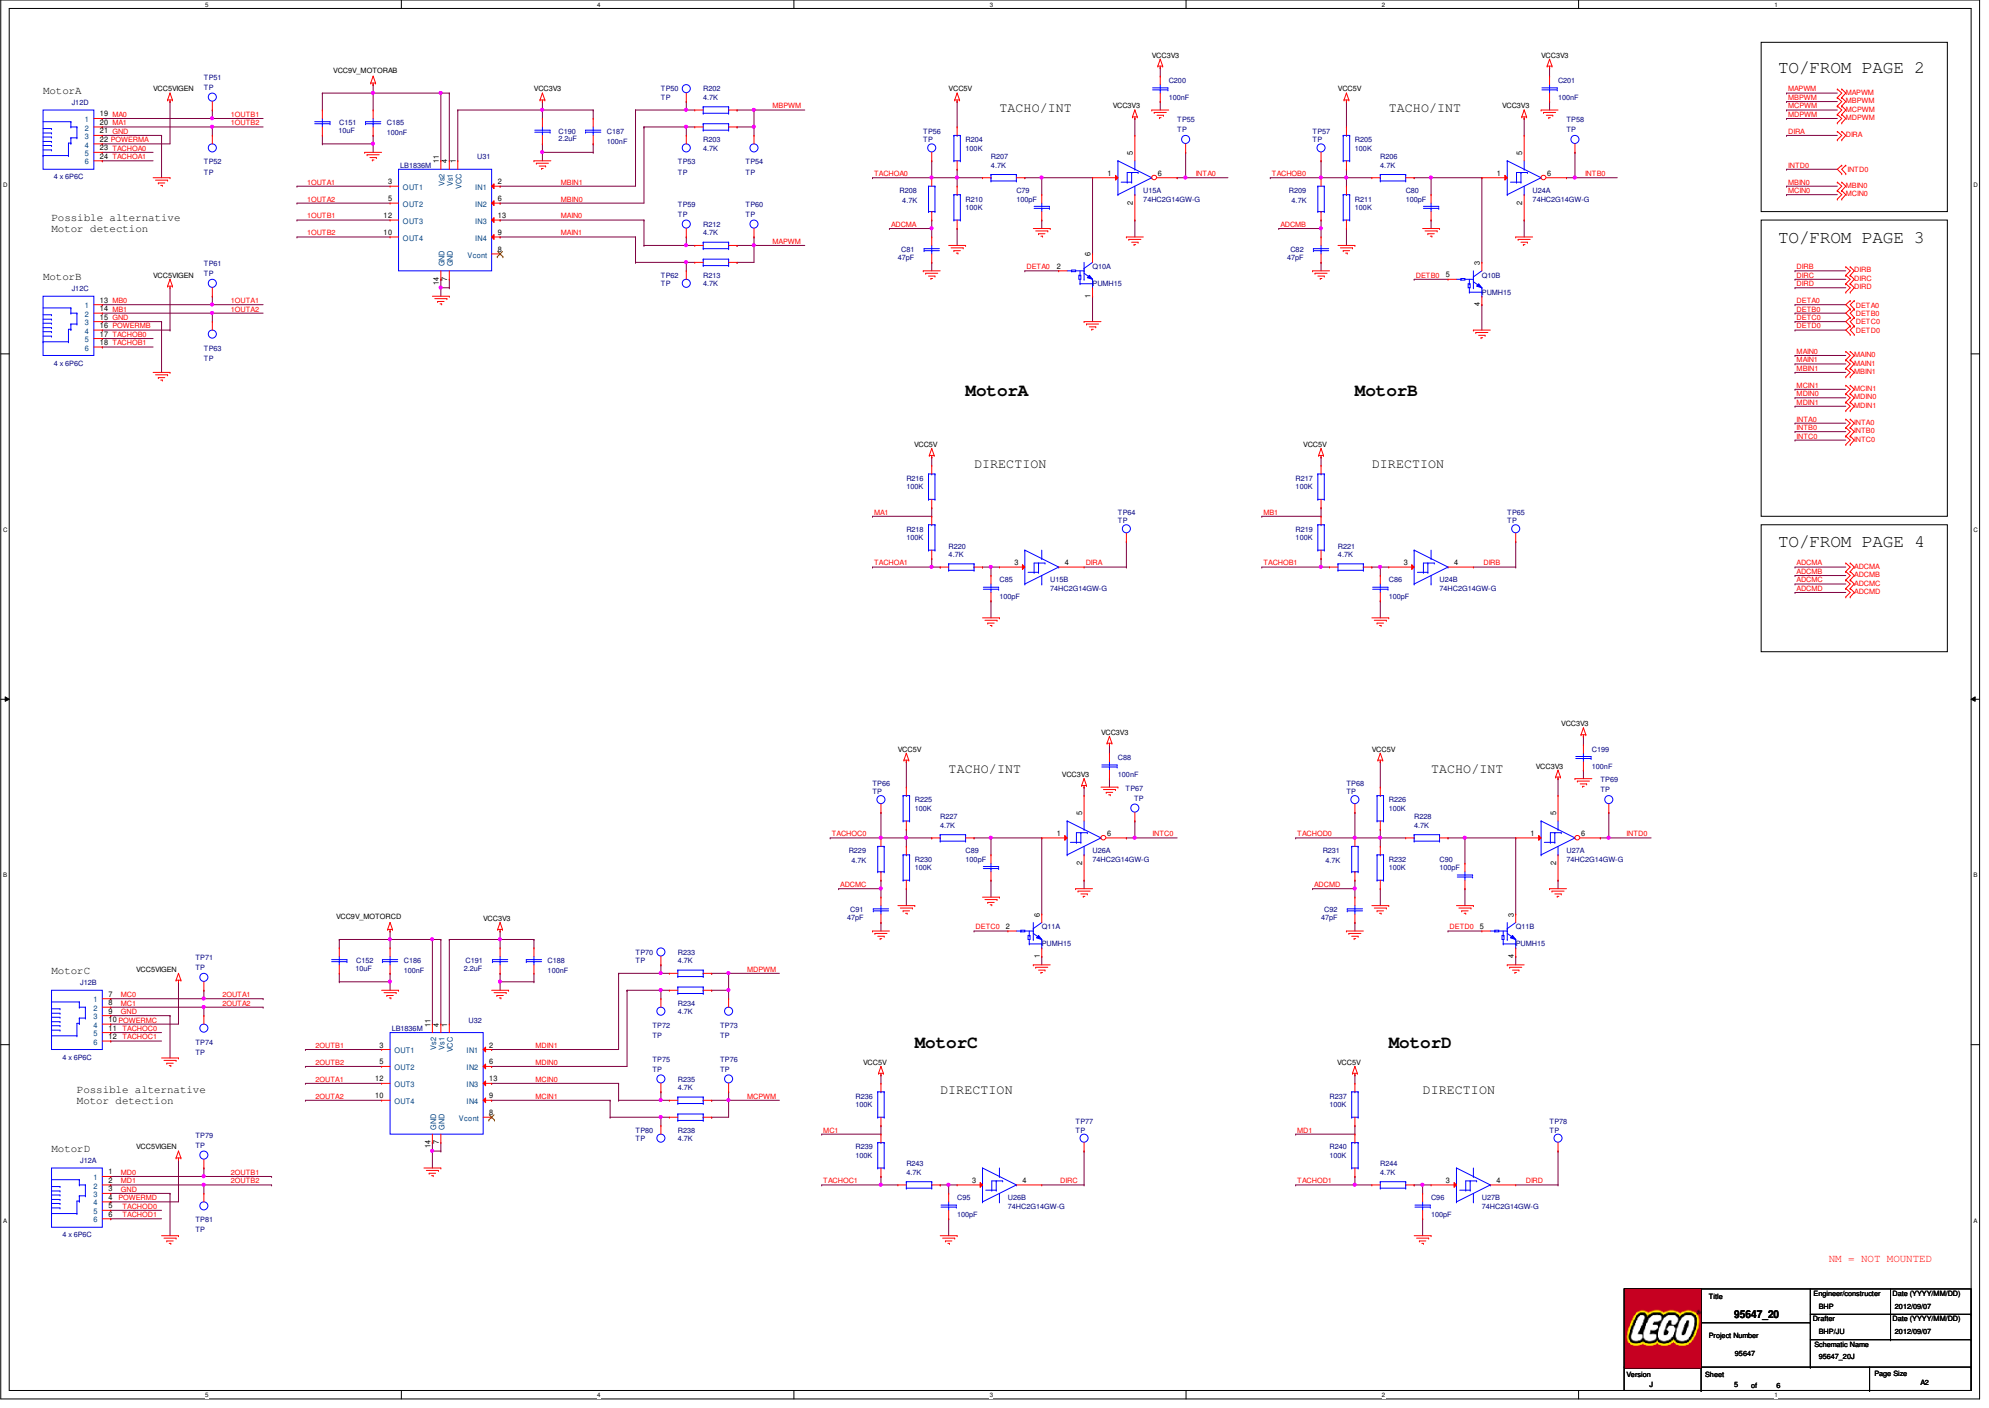
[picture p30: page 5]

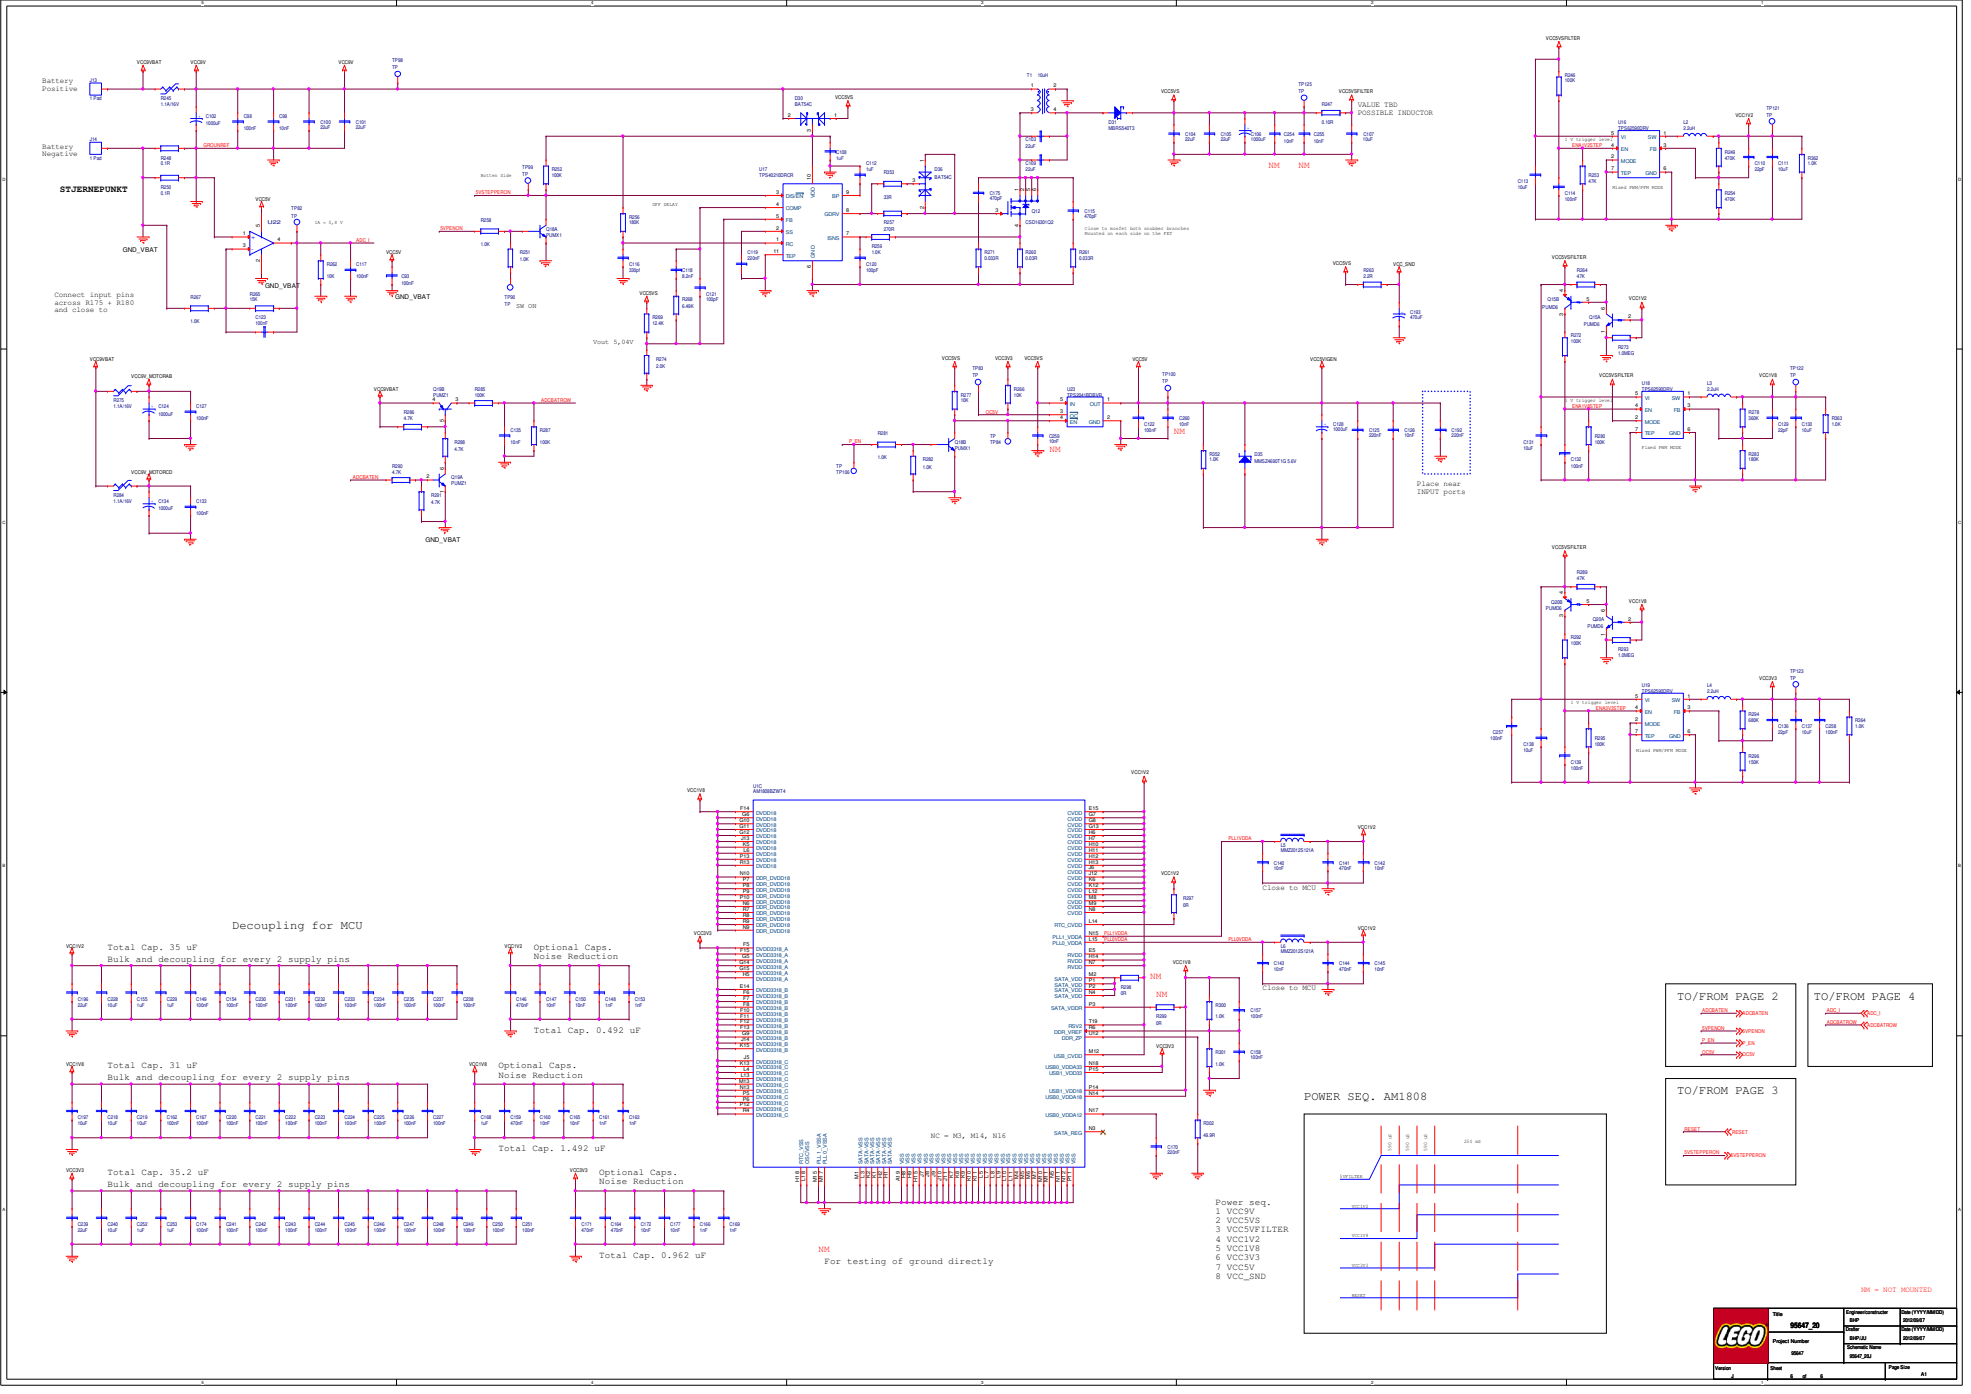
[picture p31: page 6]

Mixed PWM/PFM MODE

Close to mosfet both snubber branches
Mounted on each side on the FET

Total Cap. 35 uF
Bulk and decoupling for every 2 supply pins

For testing of ground directly

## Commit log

2025-12-23 Rename EV3 Brick schematic.pdf to EV3 Brick Schematic.pdf
2025-12-23 Rename X-UniTech Build Of Materials.pdf to X-UniTech Build Of Materials (BOM.pdf
